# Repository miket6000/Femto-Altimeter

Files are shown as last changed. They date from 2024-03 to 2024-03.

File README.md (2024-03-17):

Femto-Altimeter
================
The Femto-Altimeter is my attempt to create the smallest possible altimeter for model rocketry with the following features:
- Bluetooth LE connection to a phone to arm, check continuity and configure.
- Capable of electronic deployment.
- Altitude logging.
- Run off a single cell lithium battery, with external capacitor for deployment (if necessary).
- Be as small as possible while avoiding High Density Interconnect (uvia, etc) to allow lower cost construction.
- Designed to use parts avaialble in stock at JLCPCB at the time of design.

The resulting Femto is approximately 10x18mm (smaller than 1/2"x3/4") excluding battery. Weight will be determined when first samples arrive, but it's expected to be less than 2g.

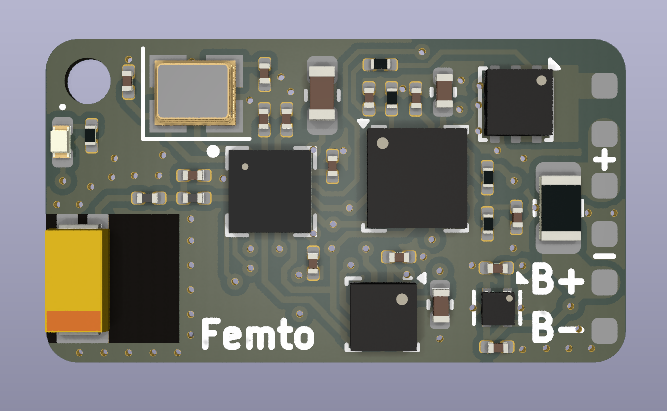
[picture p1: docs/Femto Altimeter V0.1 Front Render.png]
Front Render of Femto-Altimeter


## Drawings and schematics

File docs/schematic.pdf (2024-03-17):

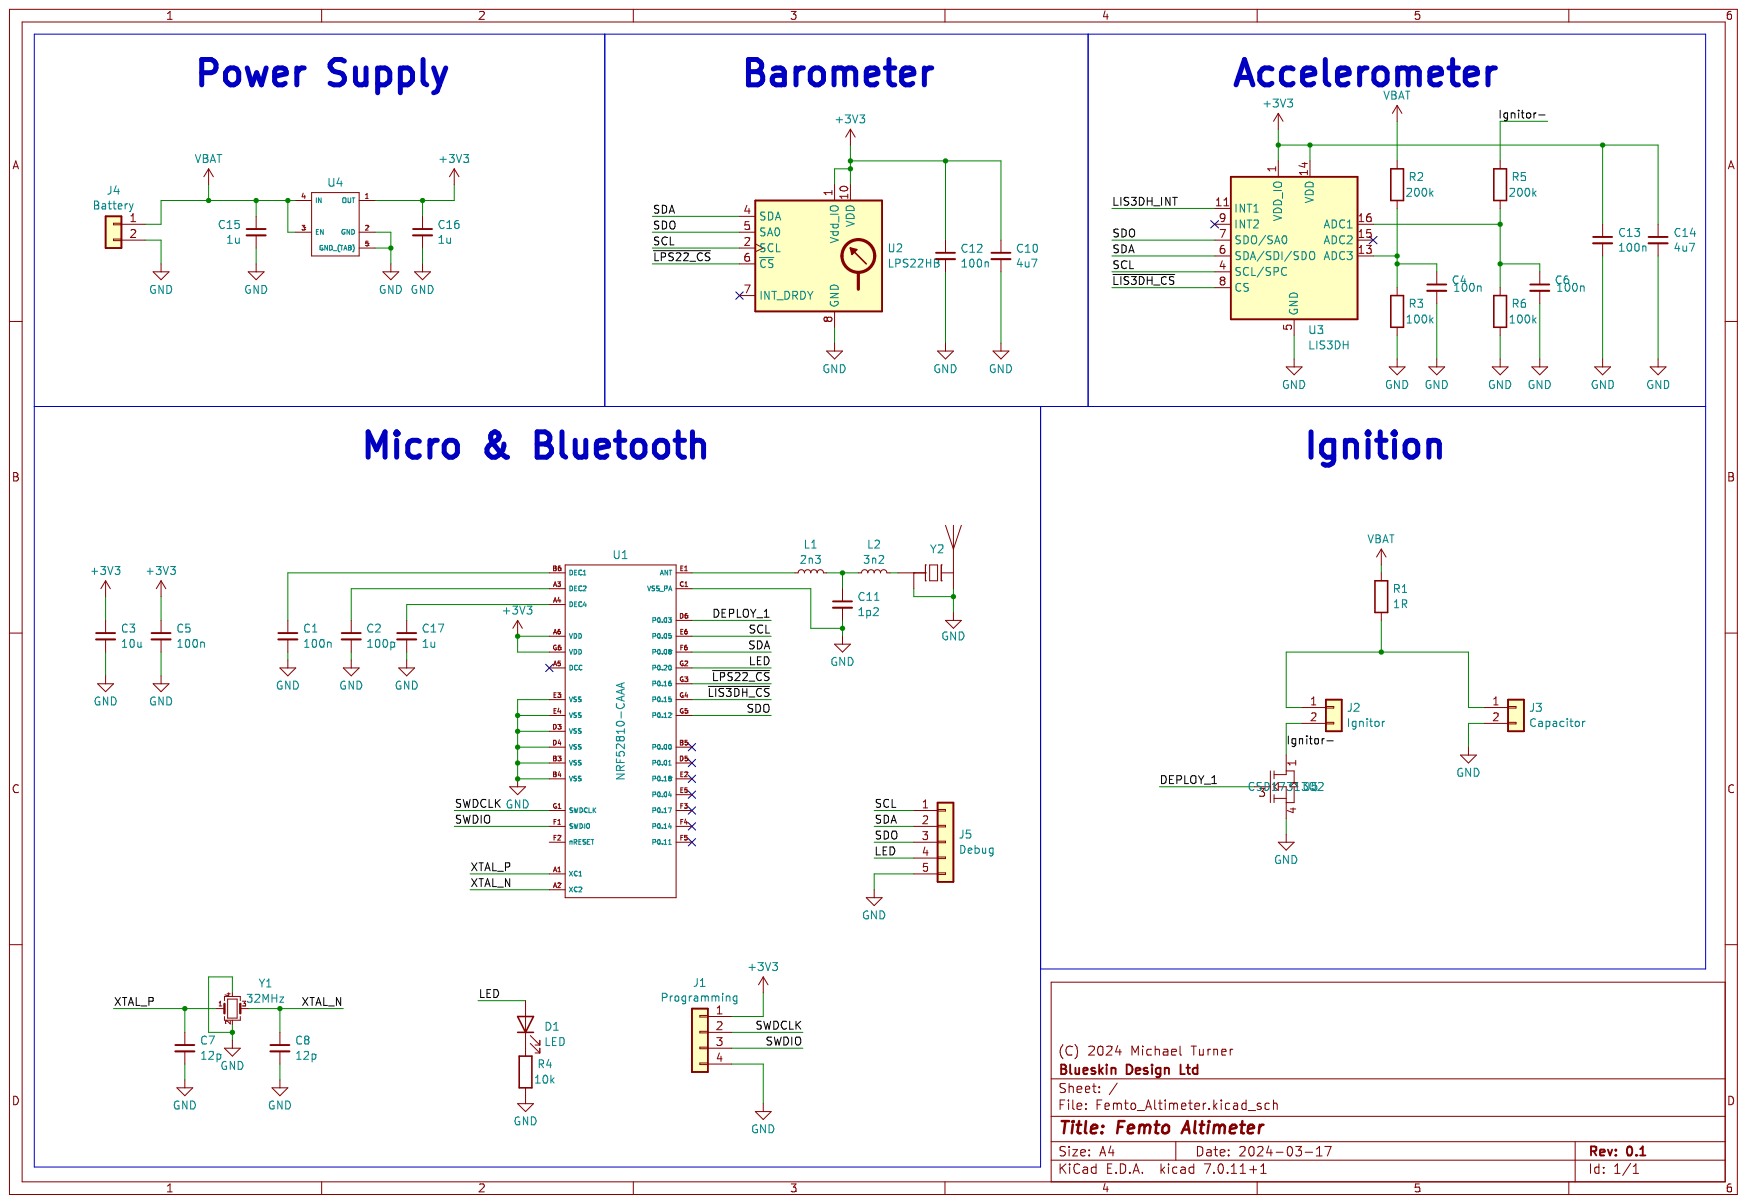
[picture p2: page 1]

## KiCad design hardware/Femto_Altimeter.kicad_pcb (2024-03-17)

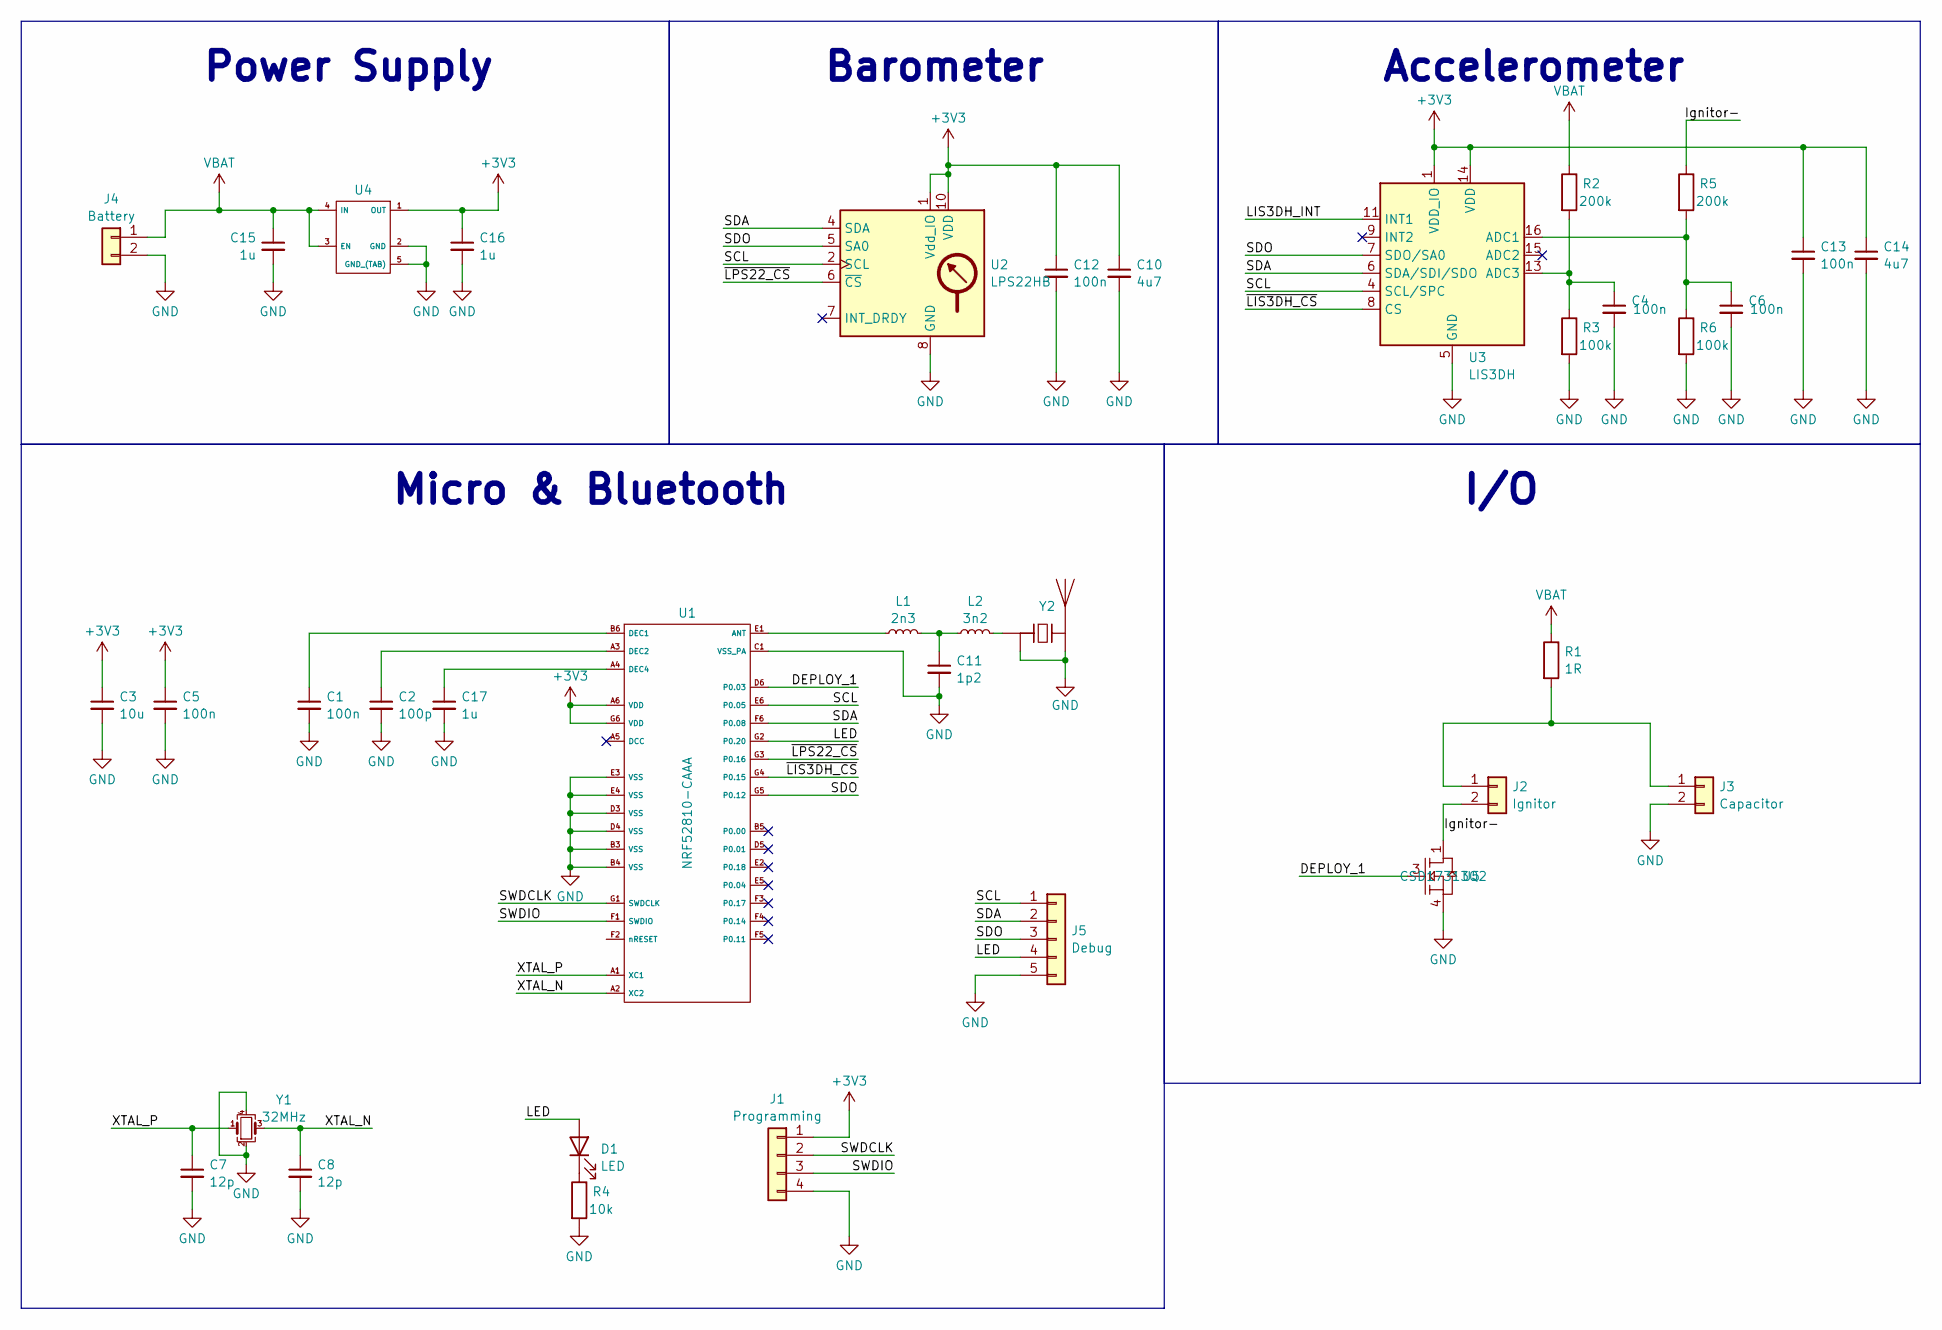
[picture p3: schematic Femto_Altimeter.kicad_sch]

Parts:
C1, C4, C5, C6, C12, C13: 100n; C_0201_0603Metric
C2: 100p; C_0201_0603Metric
C3: 10u; C_0603_1608Metric
C7, C8: 12p; C_0201_0603Metric
C10, C14: 4u7; C_0402_1005Metric
C11: 1p2; C_0201_0603Metric; JLC Part Number C1855072
C15, C16, C17: 1u; C_0201_0603Metric
D1: LED; LED_0402_1005Metric
J1: Programming; Edge_Pads_1x4_P1.0
J2: Ignitor; Edge_Pads_1x2_P1.5
J3: Capacitor; Edge_Pads_1x2_P1.5
J4: Battery; Edge_Pads_1x2_P1.5
J5: Debug; Edge_Pads_1x5_P1.0
L1: 2n3; L_0201_0603Metric; JLC Part Number C2048374
L2: 3n2; L_0201_0603Metric; JLC Part Number C408626
R1: 1R; R_0805_2012Metric
R2, R5: 200k; R_0201_0603Metric
R3, R6: 100k; R_0201_0603Metric
R4: 10k; R_0201_0603Metric
U1: NRF52810-CAAA; WLCSP-33_2.486x2.464mm; JLC Part Number C3606661
U2: LPS22HB; ST_HLGA-10_2x2mm_P0.5mm_LayoutBorder3x2y; JLC Part Number C94049
U3: LIS3DH; LGA-16_3x3mm_P0.5mm_LayoutBorder3x5y; JLC Part Number C15134
U4: OnSemi_XDFN4-1EP_1.0x1.0mm_EP0.52x0.52mm; JLC Part Number C892227
U5: CSD17313Q2; Texas_DQK; JLC Part Number C2862001
Y1: 32MHz; Crystal_SMD_2520-4Pin_2.5x2.0mm; JLC Part Number C2149238
Y2: Antenna_Chip_Pulse_Larsen_W3008; JLC Part Number C581402

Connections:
+3V3: C3.1, C5.1, C10.1, C12.1, C13.1, C14.1, C16.1, J1.1, U1.A6 (VDD), U1.G6 (VDD), U2.1 (Vdd_IO), U2.10 (VDD), U3.1 (VDD_IO), U3.14 (VDD), U4.1 (OUT)
/DEPLOY_1: U1.D6 (P0.03), U5.3 (G)
/Ignitor-: J2.2, R5.1, U5.1 (D), U5.2 (D), U5.5 (D), U5.6 (D), U5.8 (D)
/LED: D1.2 (A), J5.4, U1.G2 (P0.20)
/LIS3DH_INT: U3.11 (INT1)
/SCL: J5.1, U1.E6 (P0.05), U2.2 (SCL), U3.4 (SCL/SPC)
/SDA: J5.2, U1.F6 (P0.08), U2.4 (SDA), U3.6 (SDA/SDI/SDO)
/SDO: J5.3, U1.G5 (P0.12), U2.5 (SA0), U3.7 (SDO/SA0)
/SWDCLK: J1.2, U1.G1 (SWDCLK)
/SWDIO: J1.3, U1.F1 (SWDIO)
/XTAL_N: C8.1, U1.A2 (XC2), Y1.3
/XTAL_P: C7.1, U1.A1 (XC1), Y1.1
/~LIS3DH_CS: U1.G4 (P0.15), U3.8 (CS)
/~LPS22_CS: U1.G3 (P0.16), U2.6 (~CS)
GND: C1.2, C2.2, C3.2, C4.2, C5.2, C6.2, C7.2, C8.2, C10.2, C11.2, C12.2, C13.2, C14.2, C15.2, C16.2, C17.2, J1.4, J3.2, J4.2, J5.5, R3.2, R4.2, R6.2, U1.B3 (VSS), U1.B4 (VSS), U1.C1 (VSS_PA), U1.D3 (VSS), U1.D4 (VSS), U1.E3 (VSS), U1.E4 (VSS), U2.3 (GND), U2.8 (GND), U2.9 (GND), U3.5 (GND), U3.10 (GND), U3.12 (GND), U4.2 (GND), U4.5 (GND_(TAB)), U5.4 (S), U5.7 (S), Y1.2, Y1.4, Y2.2 (GND), Y2.3 (GND)
unnamed: C11.1, L1.1, L2.2
unnamed: D1.1 (K), R4.1
unnamed: J2.1, J3.1, R1.2
unnamed: L1.2, U1.E1 (ANT)
unnamed: C1.1, U1.B6 (DEC1)
unnamed: C2.1, U1.A3 (DEC2)
unnamed: C17.1, U1.A4 (DEC4)
unnamed: C6.1, R5.2, R6.1, U3.16 (ADC1)
unnamed: C4.1, R2.2, R3.1, U3.13 (ADC3)
unnamed: L2.1, Y2.1 (Feed)
VBAT: C15.1, J4.1, R1.1, R2.1, U4.3 (EN), U4.4 (IN)

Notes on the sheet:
Micro & Bluetooth
Barometer
I/O
Power Supply
Accelerometer

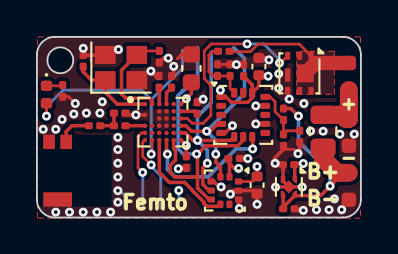
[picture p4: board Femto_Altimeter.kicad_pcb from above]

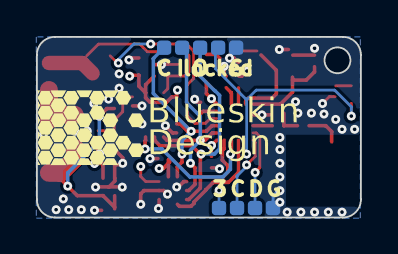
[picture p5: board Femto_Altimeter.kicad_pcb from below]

Board: 4 copper layers, 18.0 x 10.0 mm, 37 parts (2 on the bottom side), 25 nets.
